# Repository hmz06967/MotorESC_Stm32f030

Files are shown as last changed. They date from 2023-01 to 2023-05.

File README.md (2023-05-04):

# MOTOR ESC CARD DESIGN FROM EAGLE CAD

Working please download and test 

#### video (https://www.youtube.com/watch?v=FIM-RrpVAwA)

firmware https://github.com/hmz06967/MotorEsc_Firmware

## Ekran Görüntüleri

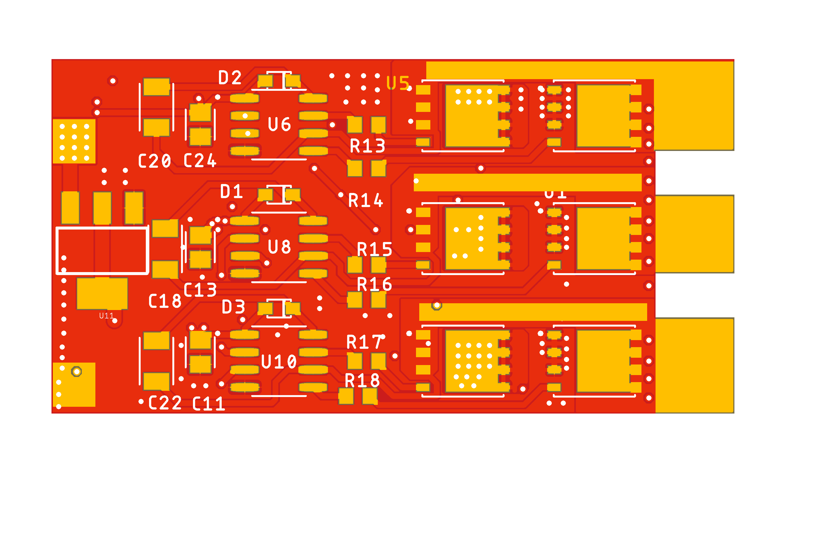
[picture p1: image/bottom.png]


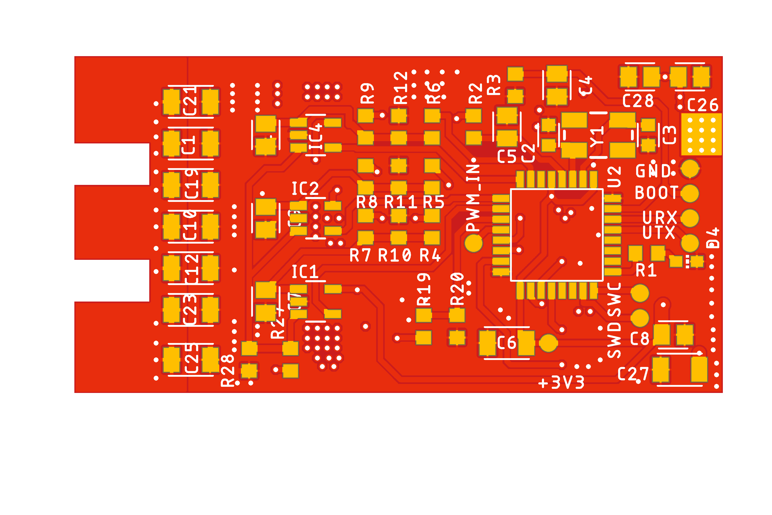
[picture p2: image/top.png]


#### Copyright (C) 2021 [OZK](https://hamzaozkan.com.tr)

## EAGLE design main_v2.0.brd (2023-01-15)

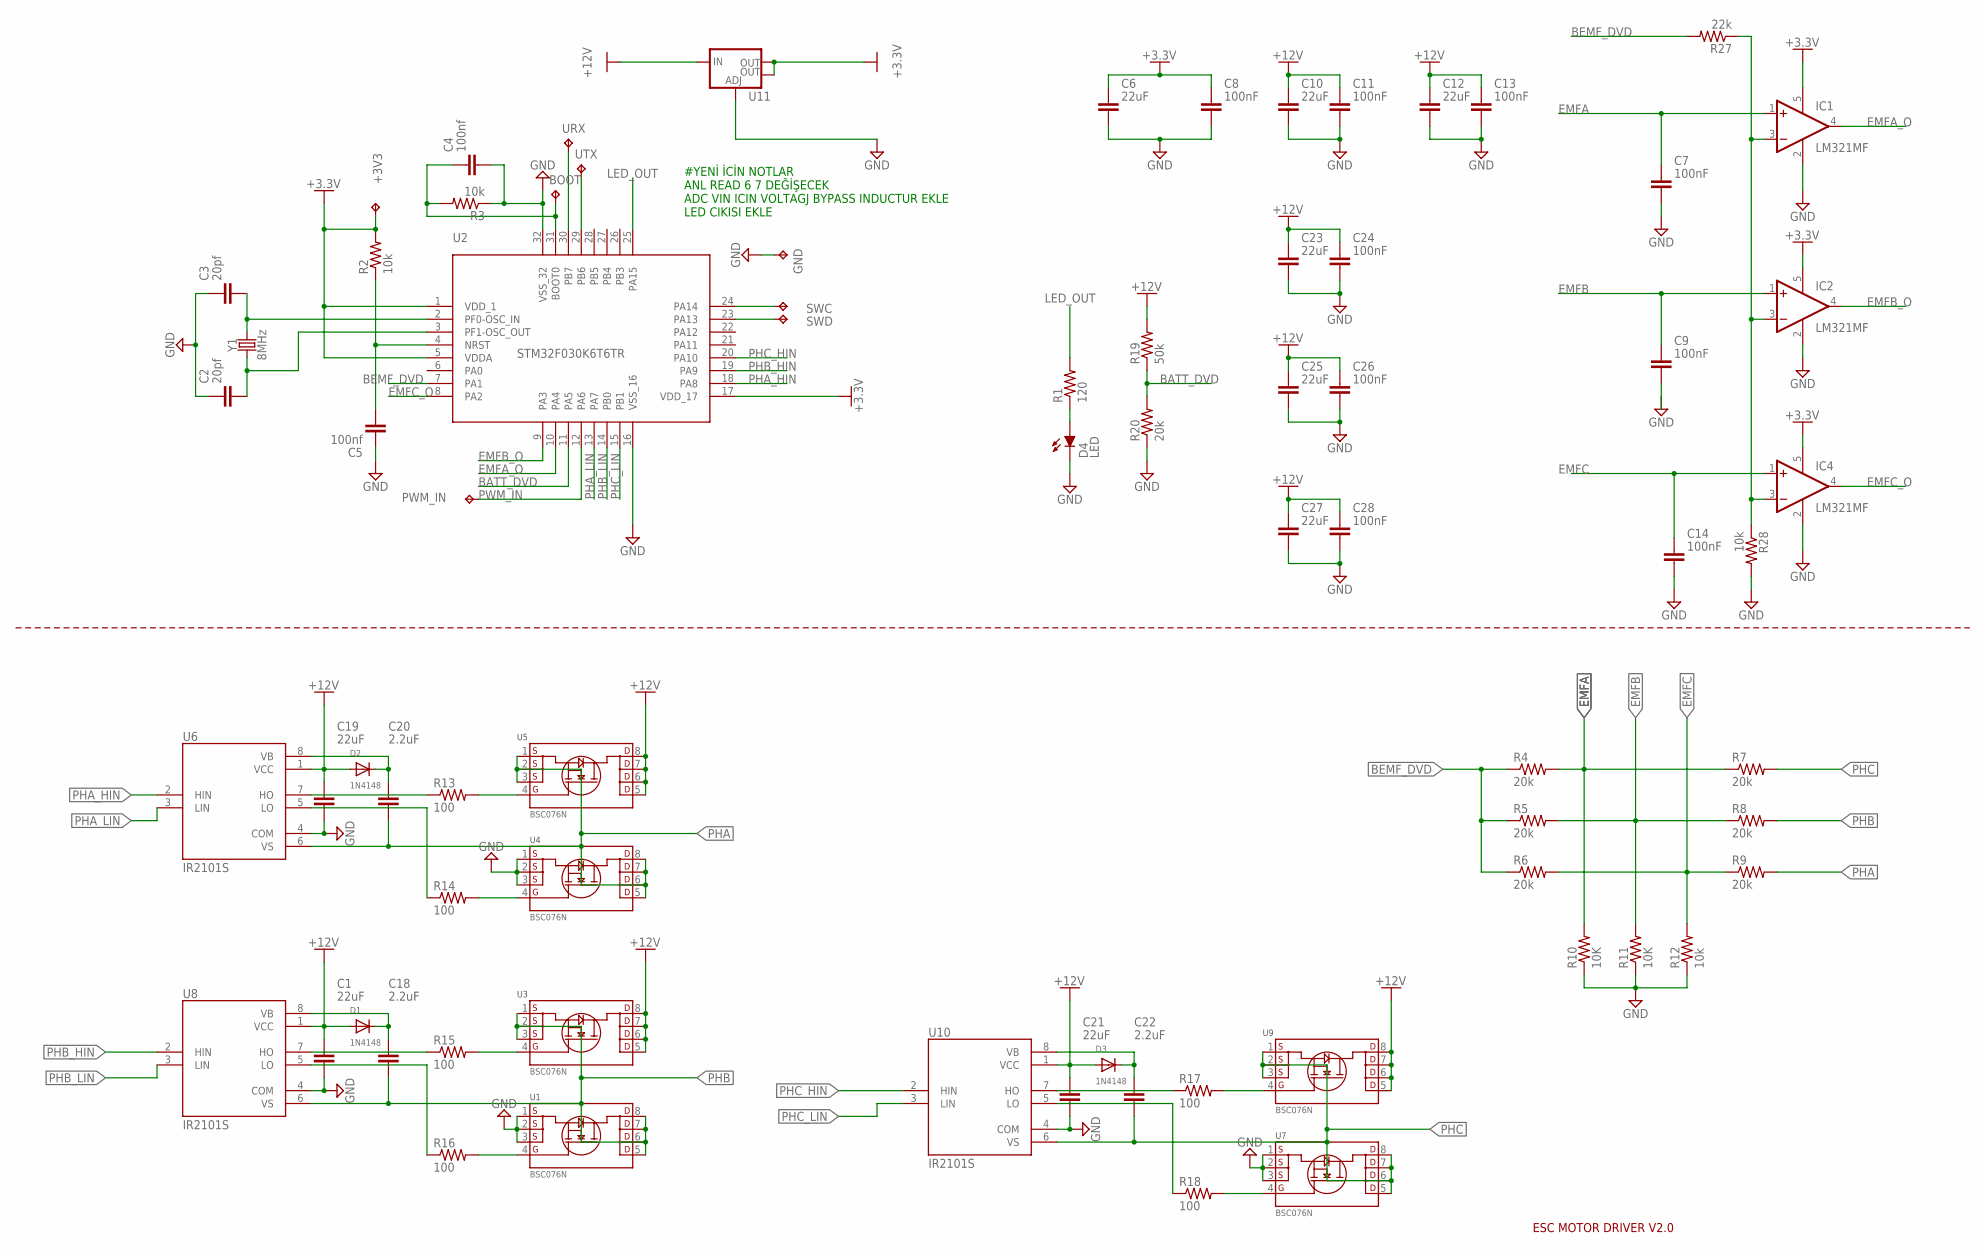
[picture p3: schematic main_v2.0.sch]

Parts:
+3V3: TPTP13R; TP13R
BOOT: TPTP13R; TP13R
C1, C6, C10, C12, C19, C21, C23, C25, C27: 22uF; CAPC3216X135
C2, C3: 20pf; CAPC1608X85
C4, C5: 100nf; CAPC2012X110
C7, C8, C9, C11, C13, C14, C24, C26, C28: 100nF; CAPC2012X110
C18, C20, C22: 2.2uF; CAPC3216X135
D1, D2, D3: 1N4148; SOD-323F
D4: LED; LED_CHIP-LED0603MP
GND: TPTP13R; TP13R
IC1, IC2, IC4: LM321MF; SOT23-5
PWM_IN: TPTP13R; TP13R
R1: 120; R0603
R2, R3, R12, R28: 10k; R0603
R4, R5, R6, R7, R8, R9, R20: 20k; R0603
R10, R11: 10K; R0603
R13, R14, R15, R16, R17, R18: 100; R0603
R19: 50k; R0603
R27: 22k; R0603
SWC: TPTP13R; TP13R
SWD: TPTP13R; TP13R
U1, U3, U4, U5, U7, U9: BSC076N; TRANS_BSC076N06NS3-G
U2: STM32F030K6T6TR; 32-LQFP
U6, U8, U10: IR2101S; SOIC127P600X175-8N
U11: V_REG_LM1117SOT223; SOT223
URX: TPTP13R; TP13R
UTX: TPTP13R; TP13R
Y1: 8MHz; CRYSTAL-SMD-5X3.2-4PAD

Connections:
+3.3V: +3V3.TP, C6.1, C8.1, IC1.5 (V+), IC2.5 (V+), IC4.5 (V+), R2.2, U2.1 (VDD_1), U2.5 (VDDA), U2.17 (VDD_17), U11.2 (OUT), U11.4 (OUT)
+12V: C1.1, C10.1, C11.1, C12.1, C13.1, C19.1, C21.1, C23.1, C24.1, C25.1, C26.1, C27.1, C28.1, D1.A, D2.A, D3.A, R19.2, U3.5 (D1), U3.6 (D2), U3.7 (D3), U3.8 (D4), U5.5 (D1), U5.6 (D2), U5.7 (D3), U5.8 (D4), U6.1 (VCC), U8.1 (VCC), U9.5 (D1), U9.6 (D2), U9.7 (D3), U9.8 (D4), U10.1 (VCC), U11.3 (IN)
BATT_DVD: R19.1, R20.2, U2.11 (PA5)
BEMF_DVD: R4.1, R5.1, R6.1, R27.2, U2.7 (PA1)
EMFA: C7.1, IC1.1 (+IN), R4.2, R7.1, R10.2
EMFA_O: IC1.4 (OUT), U2.10 (PA4)
EMFB: C9.1, IC2.1 (+IN), R5.2, R8.1, R11.2
EMFB_O: IC2.4 (OUT), U2.9 (PA3)
EMFC: C14.1, IC4.1 (+IN), R6.2, R9.1, R12.2
EMFC_O: IC4.4 (OUT), U2.8 (PA2)
GND: C1.2, C2.1, C3.1, C4.2, C5.1, C6.2, C7.2, C8.2, C9.2, C10.2, C11.2, C12.2, C13.2, C14.2, C19.2, C21.2, C23.2, C24.2, C25.2, C26.2, C27.2, C28.2, D4.C, GND.TP, IC1.2 (V-), IC2.2 (V-), IC4.2 (V-), R3.1, R10.1, R11.1, R12.1, R20.1, R28.2, U1.1 (S1), U1.2 (S2), U1.3 (S3), U2.16 (VSS_16), U2.32 (VSS_32), U4.1 (S1), U4.2 (S2), U4.3 (S3), U6.4 (COM), U7.1 (S1), U7.2 (S2), U7.3 (S3), U8.4 (COM), U10.4 (COM), U11.1 (ADJ)
LED_OUT: R1.2, U2.25 (PA15)
unnamed: C2.2, U2.3 (PF1-OSC_OUT), Y1.1
unnamed: C3.2, U2.2 (PF0-OSC_IN), Y1.3 (2)
unnamed: U2.30 (PB7), URX.TP
unnamed: C5.2, R2.1, U2.4 (NRST)
unnamed: BOOT.TP, C4.1, R3.2, U2.31 (BOOT0)
unnamed: U2.29 (PB6), UTX.TP
unnamed: IC1.3 (-IN), IC2.3 (-IN), IC4.3 (-IN), R27.1, R28.1
unnamed: SWC.TP, U2.24 (PA14)
unnamed: SWD.TP, U2.23 (PA13)
unnamed: D4.A, R1.1
unnamed: R15.1, U8.7 (HO)
unnamed: R16.1, U8.5 (LO)
unnamed: R15.2, U3.4 (G)
unnamed: C18.1, D1.C, U8.8 (VB)
unnamed: R16.2, U1.4 (G)
unnamed: R13.1, U6.7 (HO)
unnamed: R14.1, U6.5 (LO)
unnamed: C20.1, D2.C, U6.8 (VB)
unnamed: R14.2, U4.4 (G)
unnamed: R13.2, U5.4 (G)
unnamed: R17.1, U10.7 (HO)
unnamed: R18.1, U10.5 (LO)
unnamed: C22.1, D3.C, U10.8 (VB)
unnamed: R18.2, U7.4 (G)
unnamed: R17.2, U9.4 (G)
PHA: C20.2, R9.2, U4.5 (D1), U4.6 (D2), U4.7 (D3), U4.8 (D4), U5.1 (S1), U5.2 (S2), U5.3 (S3), U6.6 (VS)
PHA_HIN: U2.18 (PA8), U6.2 (HIN)
PHA_LIN: U2.13 (PA7), U6.3 (LIN)
PHB: C18.2, R8.2, U1.5 (D1), U1.6 (D2), U1.7 (D3), U1.8 (D4), U3.1 (S1), U3.2 (S2), U3.3 (S3), U8.6 (VS)
PHB_HIN: U2.19 (PA9), U8.2 (HIN)
PHB_LIN: U2.14 (PB0), U8.3 (LIN)
PHC: C22.2, R7.2, U7.5 (D1), U7.6 (D2), U7.7 (D3), U7.8 (D4), U9.1 (S1), U9.2 (S2), U9.3 (S3), U10.6 (VS)
PHC_HIN: U2.20 (PA10), U10.2 (HIN)
PHC_LIN: U2.15 (PB1), U10.3 (LIN)
PWM_IN: PWM_IN.TP, U2.12 (PA6)

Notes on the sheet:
ESC MOTOR DRIVER V2.0
#YENİ İCİN NOTLAR ANL READ 6 7 DEĞİŞECEK ADC VIN ICIN VOLTAGJ BYPASS INDUCTUR EKLE LED CIKISI EKLE

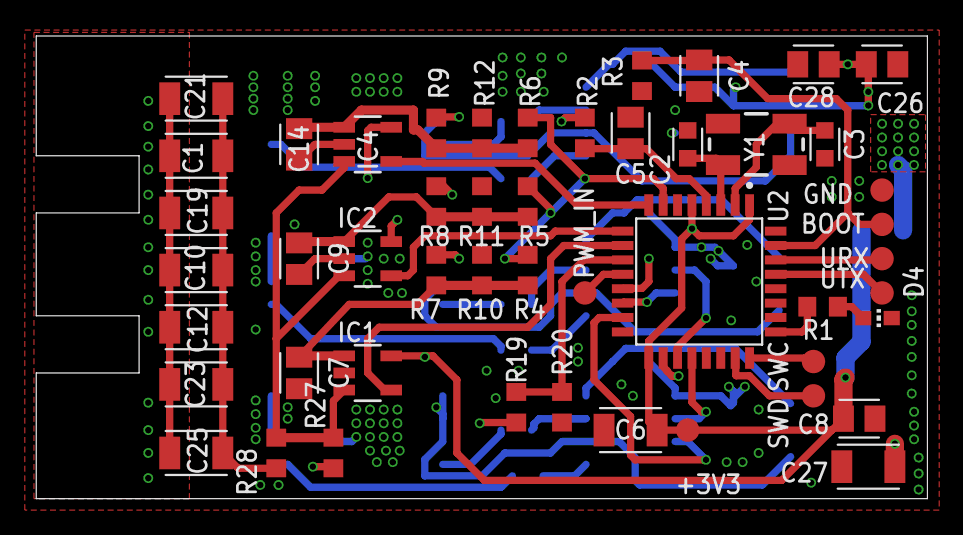
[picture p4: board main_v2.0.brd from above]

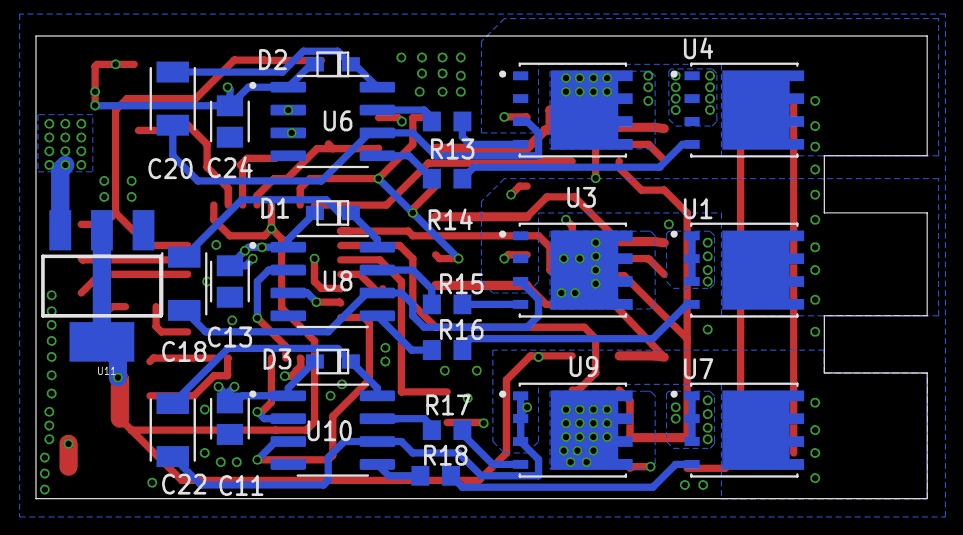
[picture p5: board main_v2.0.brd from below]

Board: 4 copper layers, 49.5 x 25.7 mm, 74 parts (25 on the bottom side), 47 nets.

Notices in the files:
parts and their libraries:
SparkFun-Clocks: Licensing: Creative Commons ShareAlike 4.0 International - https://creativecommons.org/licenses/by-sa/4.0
